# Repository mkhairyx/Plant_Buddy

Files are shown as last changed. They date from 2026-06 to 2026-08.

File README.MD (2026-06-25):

# Plant Buddy
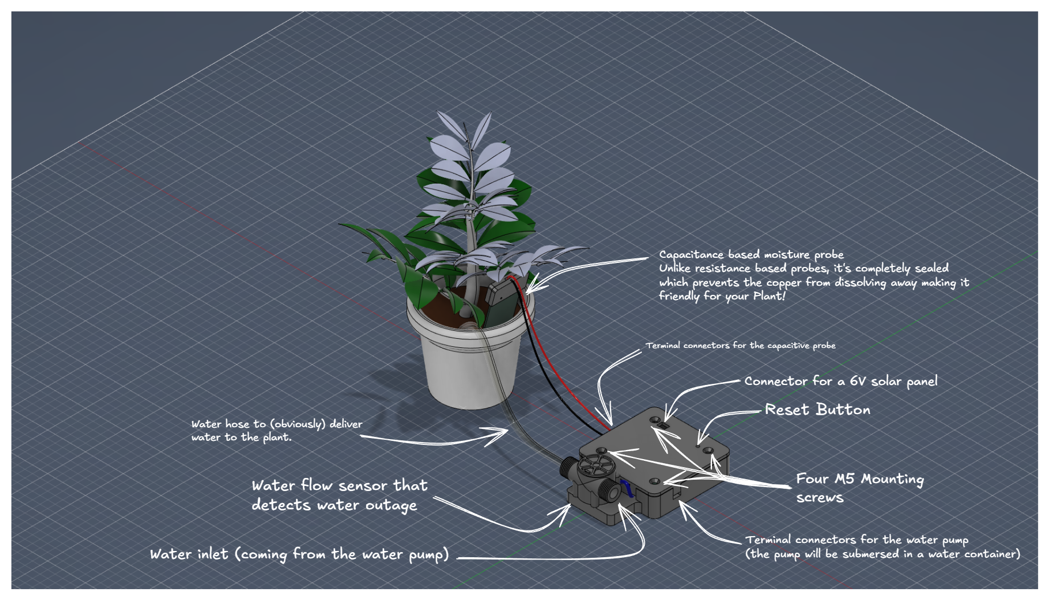
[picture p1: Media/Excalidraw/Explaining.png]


## The reason I made it
I have a plant at a remote location and I only go there once in a while, I was afraid that that plant might die because of the lack of water so I decided to make this device. It work by connecting a water pump to it, then it drives this pump every 20 days by default (configurable in the code). It measures the soil humidity for feedback to the user (which is delivered through SMS).

## The poster
zine

## Photos

|Schematic |PCB |3D View |Showcase |
|---|---|---|---|
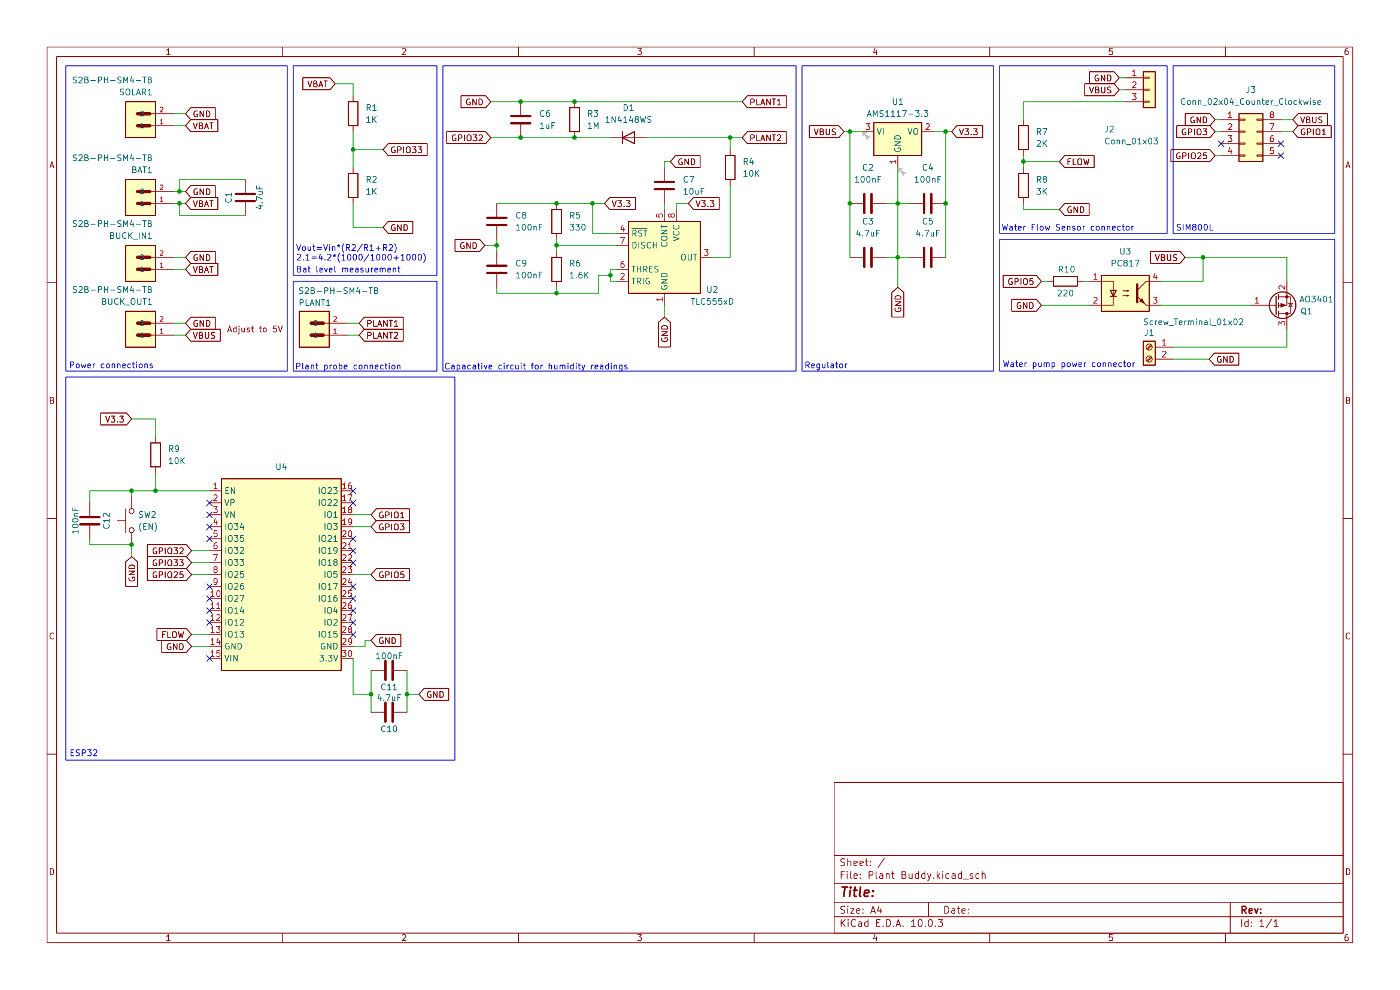
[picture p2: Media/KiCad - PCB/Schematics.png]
Schematics
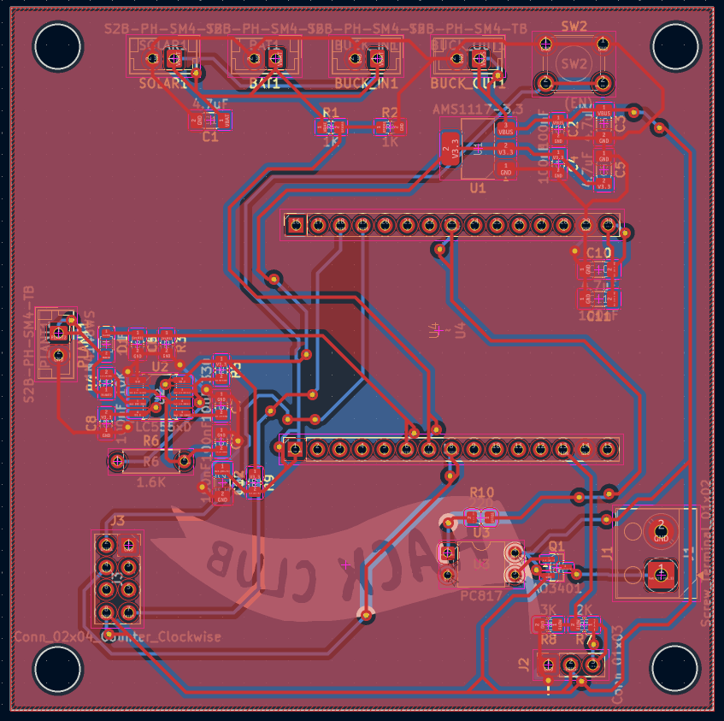
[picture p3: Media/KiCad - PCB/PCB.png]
PCB
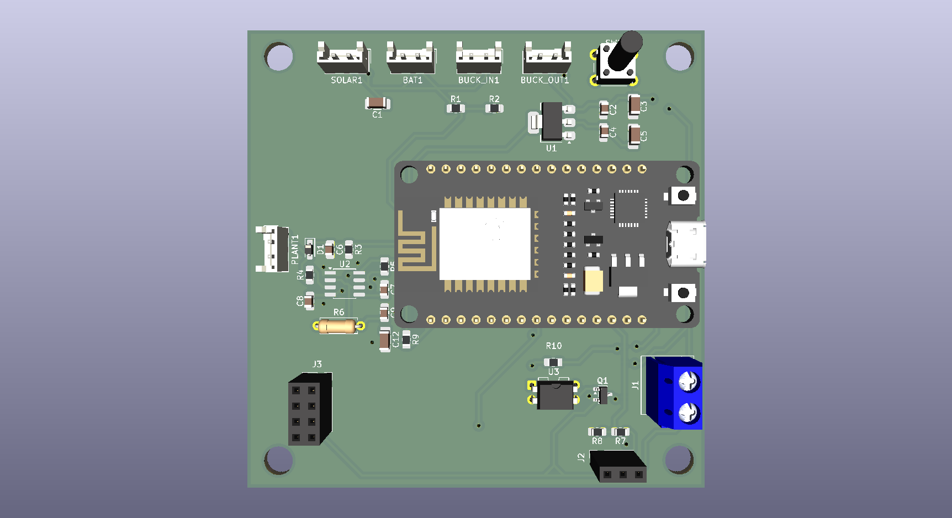
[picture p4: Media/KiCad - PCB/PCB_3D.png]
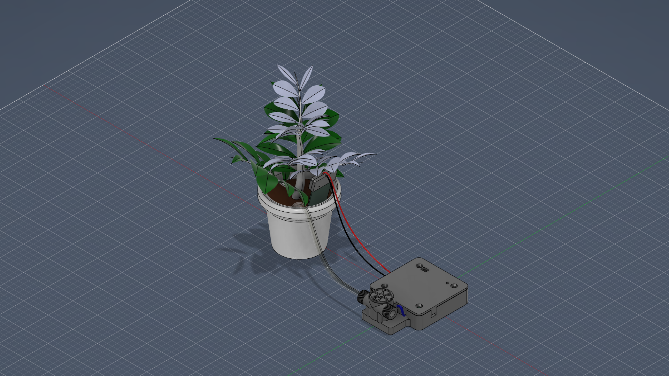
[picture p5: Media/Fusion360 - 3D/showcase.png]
Showcase
|||||

## Step files
All of the step files can be found [here](./Step_Files/).
<br>

## Firmware
### Compile and flash using the Arduino IDE
If you want to edit the code, compile it yourself, then flash it; you can download the arduino sketch [here](./Source/Firmware/Arduino/plant_buddy).

### Flash the firmware as is
If you want to flash the firmware as is, you can download it [here](./source/Firmware/Firmware). <br>
You can use [ESPWebTool](https://esptool.spacehuhn.com) to flash the firmware directly to the ESP32 using your browser.<br>
Note that there might be some changes between the Arduino code and the firmware as some changes were made.

## Device Operation
### Power supply
The device is powered a 3.7V recharge Li-Po battery.<br>
The battery is recharged daily using a 3W 6V mini solar panel connected to a mini solar charger which is connected to a buck converter to operate the ESP32.<br>
The ESP32 goes into Deep Sleep mode in between watering sessions to help decrease energy consumption.<br>

### Startup Notification

Whenever the ESP32 wakes up, it sends a status report to the user containing:

* Current battery level
* Current soil moisture level
* Watering interval
* Reason for waking up

Example:

```
The device just booted up!
Battery level: 87%
Soil humidity: 42%
Watering interval: 3 days

Boot reason: Watering cycle completed successfully.
Watering again in 3 days.
```

Possible boot reasons:

| Boot Reason | Description |
| --- | --- |
| Unknown Fault | The device restarted unexpectedly due to an unknown error. |
| Watering Cycle Completed | A watering cycle has just finished successfully, and a new countdown has started. |
| First Boot | The device has been powered on for the first time. |

## BOM
### BOM Table (components only)
|Name |Link |Cost per one (EGP) |Cost per one (USD) |Amount |Total cost|
|---|---|---|---|---|---|
|JST Connectors |https://www.ram-e-shop.com/shop/pw-m-pcb-2pin-pw-m-2-pin-polarized-male-jst-xh2-54-connector-for-pcb-6463| EGP 0.60 | $0.012 |5 | $0.060 |
|4.7uF Caps (1206) |https://lampatronics.com/product/smd-multilayer-ceramic-capacitor-1206-4-7uf-16v-1pcs| EGP 1.50 | $0.030 |4 | $0.120 |
|100nF Caps (0805) |https://lampatronics.com/product/smd-multilayer-ceramic-capacitor-0805-2012-104-100nf-50v-1pcs-2| EGP 1.00 | $0.020 |6 | $0.120 |
|1uF Caps (0805) |https://lampatronics.com/product/smd-ceramic-capacitor-0805-1051uf-50v-1pcs| EGP 1.50 | $0.030 |1 | $0.030 |
|10uF Caps (0805) |https://lampatronics.com/product/smd-multilayer-ceramic-capacitor-0805-10610uf-16v-1pcs| EGP 1.50 | $0.030 |1 | $0.030 |
|1N4148WS Diode |https://lampatronics.com/product/smd-diode-1n4148ws-10pcs| EGP 7.50 | $0.150 |1 | $0.150 |
|Screw terminal |https://www.ram-e-shop.com/shop/r-3-roseta-2pin-2-pin-pcb-screw-terminal-block-pitch-5mm-r-3-5854| EGP 3.00 | $0.060 |1 | $0.060 |
|Male headers |https://store.fut-electronics.com/products/male-pin-headers-standard-2-54-mm-40-pin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| EGP 10.00 | $0.200 |1 | $0.200 |
|Female headers |https://www.ram-e-shop.com/shop/ph35-1x4-female-ph35-pin-header-female-1x4-straight-2-54mm-6976| EGP 1.50 | $0.030 |2 | $0.060 |
|AO3401 (transistor for pump) |https://uge-one.com/product/ao3401-sot23-general-purpose-p-channel-mosfet-smd-transistor-sot-23/| EGP 3.00 | $0.060 |1 | $0.060 |
|1K ohm Resistors |https://lampatronics.com/product/smd-resistor-1kohm-102-0805-10pcs| EGP 2.00 | $0.040 |1 | $0.040 |
|1M ohm Resistors |https://lampatronics.com/product/smd-resistor-1mohm-105-0805-10pcs| EGP 2.00 | $0.040 |1 | $0.040 |
|10K ohm Resistors |https://lampatronics.com/product/smd-resistor-10kohm-103-0805-10pcs| EGP 2.00 | $0.040 |1 | $0.040 |
|330 ohm Resistors |https://lampatronics.com/product/smd-resistor-330ohm-331-0805-10pcs| EGP 2.00 | $0.040 |1 | $0.040 |
|1.5Kohm Resistors |https://lampatronics.com/product/resistor-1-5k-ohm-1-4w-4pcs-2| EGP 0.30 | $0.006 |1 | $0.006 |
|2K ohm Resistors |https://lampatronics.com/product/smd-resistor-2kohm-202-0805-10pcs| EGP 2.00 | $0.040 |1 | $0.040 |
|3K ohm Resistors |https://lampatronics.com/product/smd-resistor-3kohm-302-0805-10pcs| EGP 2.00 | $0.040 |1 | $0.040 |
|220 ohm Resistors |https://lampatronics.com/product/smd-resistor-220ohm-221-0805-10pcs| EGP 2.00 | $0.040 |1 | $0.040 |
|Reset Push Button |https://lampatronics.com/product/push-button-4pin-long-6x6x13mm| EGP 1.50 | $0.030 |1 | $0.030 |
|Voltage Regulator |https://lampatronics.com/product/ams1117-33v-sot-223-33v-linear-voltage-regulator| EGP 2.00 | $0.040 |1 | $0.040 |
|TLC555xD (Capacitive soil readings) |https://uge-one.com/product/tlc555cdr-low-power-cmos-timer-ic-smd-sop8/| EGP 35.00 | $0.700 |1 | $0.700 |
|PC817 optocoupler |https://lampatronics.com/product/pc817-optocoupler-dip-4| EGP 1.25 | $0.025 |1 | $0.025 |
|ESP32 DevKit |https://lampatronics.com/product/esp32-30pin-development-board-wifi-and-bluetooth| EGP 325.00 | $6.500 |1 | $6.500 |
|Water Pump |https://www.ram-e-shop.com/shop/dc-pump-6vdc-water-pump-3-6vdc-mini-120l-h-7422| EGP 45.00 | $0.900 |1 | $0.900 |
|Hose (inner d: 6mm , outer d: 8mm) 1 Meter |https://lampatronics.com/product/flexible-clear-hose-tube-pipe-6mm-airwater-pump-pvc| EGP 15.00 | $0.300 |2 | $0.600 |
|Water Flow sensor |https://store.fut-electronics.com/products/water-flow-rate-sensor?_pos=8&_sid=5e9c09df8&_ss=r| EGP 260.00 | $5.200 |1 | $5.200 |
|SIM800L GSM Module |https://store.fut-electronics.com/collections/gsm-gprs/products/sim800l-gprs-gsm-module-esp-core-board-with-built-in-antenna| EGP 280.00 | $5.600 |1 | $5.600 |
|3W 6V Mini Solar Panel |https://store.fut-electronics.com/products/solar-cell-129-x-129-mm-3w?_pos=3&_sid=fdb2b11fe&_ss=r| EGP 155.00 | $3.100 |1 | $3.100 |
|Mini solar charger |https://store.fut-electronics.com/products/solar-usb-charger-for-lithium-batteries-lipo-rider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| EGP 160.00 | $3.200 |1 | $3.200 |
|Battery |https://store.fut-electronics.com/products/3-7v-rechargeable-polymer-lithium-ion-battery-ecocell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| EGP 125.00 | $2.500 |1 | $2.500 |
|M5 Screws |https://store.fut-electronics.com/products/screw-m5x25mm-hexagonal-head?_pos=5&_sid=c4191184f&_ss=r| EGP 2.00 | $0.040 |4 | $0.160 |
| | | | | | |
| | | | |Whole Total| $29.731  |

### Quotes
[JLCPCB](https://jlcpcb.com) : $57.12
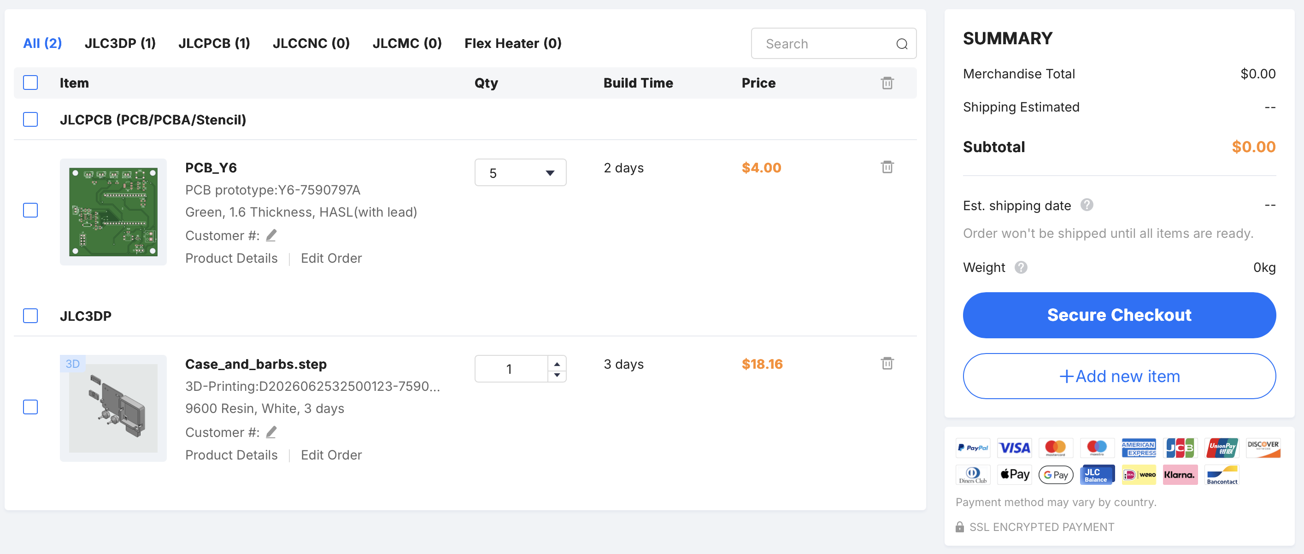
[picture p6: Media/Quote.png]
Quote

<br>
Note that local manufacturers might have different prices.

## Notes
A future V2 is planned with support for multiple probes, improved power efficiency, and user-requested status updates.

> Made and designed by [@mkhairyx](https://github.com/mkhairyx).<br>
Supported by [Fallout](https://fallout.hackclub.com/) and [Hack Club](https://hackclub.com).<br>

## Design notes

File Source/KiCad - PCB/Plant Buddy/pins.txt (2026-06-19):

gpio 33 for battery voltage -
gpio 32 for soil readings -
gpio 5 for pump motor -
gpio 3 for gsm_tx -
gpio 1 for gsm_rx -
gpio 13 for flow -
gpio 25 for ring ping -

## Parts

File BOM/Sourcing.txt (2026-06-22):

- water pump: https://www.ram-e-shop.com/shop/dc-pump-6vdc-water-pump-3-6vdc-mini-120l-h-7422
- hose: https://lampatronics.com/product/flexible-clear-hose-tube-pipe-6mm-airwater-pump-pvc
- Flow sensor: https://store.fut-electronics.com/products/water-flow-rate-sensor?_pos=8&_sid=5e9c09df8&_ss=r
- SIM800L: https://store.fut-electronics.com/collections/gsm-gprs/products/sim800l-gprs-gsm-module-esp-core-board-with-built-in-antenna
- 6w solar: https://store.fut-electronics.com/products/solar-cell-129-x-129-mm-3w?_pos=3&_sid=fdb2b11fe&_ss=r
- Mini solar charger: https://store.fut-electronics.com/products/solar-usb-charger-for-lithium-batteries-lipo-rider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
- JST: https://www.ram-e-shop.com/shop/pw-m-pcb-2pin-pw-m-2-pin-polarized-male-jst-xh2-54-connector-for-pcb-6463
step up module: https://lampatronics.com/product/dc-dc-step-up-boost-converter-module-xl6009-3a
1N4148WS: https://makerselectronics.com/product/smd-switching-diode-1n4148ws-t4-100v-independent-type-1-25v150ma-4ns-150ma-sod-323/
- 555: https://uge-one.com/product/tlc555cdr-low-power-cmos-timer-ic-smd-sop8/
- terminal connector: https://www.ram-e-shop.com/shop/r-3-roseta-2pin-2-pin-pcb-screw-terminal-block-pitch-5mm-r-3-5854
- Female headers : https://www.ram-e-shop.com/shop/ph35-1x4-female-ph35-pin-header-female-1x4-straight-2-54mm-6976
- 4.7uF: https://lampatronics.com/product/smd-multilayer-ceramic-capacitor-1206-4-7uf-16v-1pcs
- 100nF: https://lampatronics.com/product/smd-multilayer-ceramic-capacitor-0805-2012-104-100nf-50v-1pcs-2
- 1uF: https://lampatronics.com/product/smd-ceramic-capacitor-0805-1051uf-50v-1pcs
- 10uF: https://lampatronics.com/product/smd-multilayer-ceramic-capacitor-0805-10610uf-16v-1pcs
- 1N4148WS: https://lampatronics.com/product/smd-diode-1n4148ws-10pcs
- AO3401: https://uge-one.com/product/ao3401-sot23-general-purpose-p-channel-mosfet-smd-transistor-sot-23/
- 1Kohm: https://lampatronics.com/product/smd-resistor-1kohm-102-0805-10pcs
- 1Mohm: https://lampatronics.com/product/smd-resistor-1mohm-105-0805-10pcs
- 10Kohm: https://lampatronics.com/product/smd-resistor-10kohm-103-0805-10pcs
- 330ohm: https://lampatronics.com/product/smd-resistor-330ohm-331-0805-10pcs
- 1.5Kohm: https://lampatronics.com/product/resistor-1-5k-ohm-1-4w-4pcs-2
- 2Kohm: https://lampatronics.com/product/smd-resistor-2kohm-202-0805-10pcs
- 3Kohm: https://lampatronics.com/product/smd-resistor-3kohm-302-0805-10pcs
- 220ohm : https://lampatronics.com/product/smd-resistor-220ohm-221-0805-10pcs
- RST button: https://lampatronics.com/product/push-button-4pin-long-6x6x13mm
- AMS1117-3.3: https://lampatronics.com/product/ams1117-33v-sot-223-33v-linear-voltage-regulator
- PC817: https://lampatronics.com/product/pc817-optocoupler-dip-4
- ESP32: https://lampatronics.com/product/esp32-30pin-development-board-wifi-and-bluetooth
- Battery: https://store.fut-electronics.com/products/3-7v-rechargeable-polymer-lithium-ion-battery-ecocell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
- four M5 screws: https://store.fut-electronics.com/products/screw-m5x25mm-hexagonal-head?_pos=5&_sid=c4191184f&_ss=r

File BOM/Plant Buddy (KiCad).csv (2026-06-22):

Reference | Qty | Value | Footprint
BAT1,BUCK_IN1,BUCK_OUT1,PLANT1,SOLAR1 | 5 | S2B-PH-SM4-TB | Connector_JST:JST_EH_B2B-EH-A_1x02_P2.50mm_Vertical
C1,C3,C5,C10 | 4 | 4.7uF | Capacitor_SMD:C_1206_3216Metric_Pad1.33x1.80mm_HandSolder
C2,C4,C8,C9 | 4 | 100nF | Capacitor_SMD:C_0805_2012Metric_Pad1.18x1.45mm_HandSolder
C6 | 1 | 1uF | Capacitor_SMD:C_0805_2012Metric_Pad1.18x1.45mm_HandSolder
C7 | 1 | 10uF | Capacitor_SMD:C_0805_2012Metric_Pad1.18x1.45mm_HandSolder
C11,C12 | 2 | 100nF | Capacitor_SMD:C_1206_3216Metric_Pad1.33x1.80mm_HandSolder
D1 | 1 | 1N4148WS | Diode_SMD:D_SOD-323_HandSoldering
J1 | 1 | Screw_Terminal_01x02 | TerminalBlock_Altech:Altech_AK100_1x02_P5.00mm
J2 | 1 | Conn_01x03 | Connector_PinSocket_2.54mm:PinSocket_1x03_P2.54mm_Vertical
J3 | 1 | Conn_02x04_Counter_Clockwise | Connector_PinSocket_2.54mm:PinSocket_2x04_P2.54mm_Vertical
Q1 | 1 | AO3401 | Package_TO_SOT_SMD:SOT-23
R1,R2 | 2 | 1K | Resistor_SMD:R_0805_2012Metric_Pad1.20x1.40mm_HandSolder
R3 | 1 | 1M | Resistor_SMD:R_0805_2012Metric_Pad1.20x1.40mm_HandSolder
R4,R9 | 2 | 10K | Resistor_SMD:R_0805_2012Metric_Pad1.20x1.40mm_HandSolder
R5 | 1 | 330 | Resistor_SMD:R_0805_2012Metric_Pad1.20x1.40mm_HandSolder
R6 | 1 | 1.6K | Resistor_THT:R_Axial_DIN0207_L6.3mm_D2.5mm_P7.62mm_Horizontal
R7 | 1 | 2K | Resistor_SMD:R_0805_2012Metric_Pad1.20x1.40mm_HandSolder
R8 | 1 | 3K | Resistor_SMD:R_0805_2012Metric_Pad1.20x1.40mm_HandSolder
R10 | 1 | 220 | Resistor_SMD:R_0805_2012Metric_Pad1.20x1.40mm_HandSolder
SW2 | 1 | (EN) | Button_Switch_THT:SW_PUSH_6mm_H13mm
U1 | 1 | AMS1117-3.3 | Package_TO_SOT_SMD:SOT-223-3_TabPin2
U2 | 1 | TLC555xD | Package_SO:SOP-8_3.76x4.96mm_P1.27mm
U3 | 1 | PC817 | Package_DIP:DIP-4_W7.62mm
U4 | 1 |  | Library:ESP32 DevKit

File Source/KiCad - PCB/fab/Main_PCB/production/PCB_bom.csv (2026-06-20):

Designator | Footprint | Quantity | Value | LCSC Part #
BAT1, BUCK_IN1, BUCK_OUT1, PLANT1, SOLAR1 | JST_EH_B2B-EH-A_1x02_P2.50mm_Vertical | 5 | S2B-PH-SM4-TB
C1, C10, C3, C5 | 1206 | 4 | 4.7uF
C11, C12 | 1206 | 2 | 100nF
C2, C4, C8, C9 | 0805 | 4 | 100nF
C6 | 0805 | 1 | 1uF
C7 | 0805 | 1 | 10uF
D1 | D_SOD-323_HandSoldering | 1 | 1N4148WS
J1 | Altech_AK100_1x02_P5.00mm | 1 | Screw_Terminal_01x02
J2 | PinSocket_1x03_P2.54mm_Vertical | 1 | Conn_01x03
J3 | PinSocket_2x04_P2.54mm_Vertical | 1 | Conn_02x04_Counter_Clockwise
Q1 | SOT-23 | 1 | AO3401
R1, R2 | 0805 | 2 | 1K
R10 | 0805 | 1 | 220
R3 | 0805 | 1 | 1M
R4, R9 | 0805 | 2 | 10K
R5 | 0805 | 1 | 330
R6 | R_Axial_DIN0207_L6.3mm_D2.5mm_P7.62mm_Horizontal | 1 | 1.6K
R7 | 0805 | 1 | 2K
R8 | 0805 | 1 | 3K
SW2 | SW_PUSH_6mm_H13mm | 1 | (EN)
U1 | SOT-223-3_TabPin2 | 1 | AMS1117-3.3
U2 | SOP-8_3.76x4.96mm_P1.27mm | 1 | TLC555xD
U3 | DIP-4_W7.62mm | 1 | PC817
U4 | ESP32 DevKit | 1 | ~

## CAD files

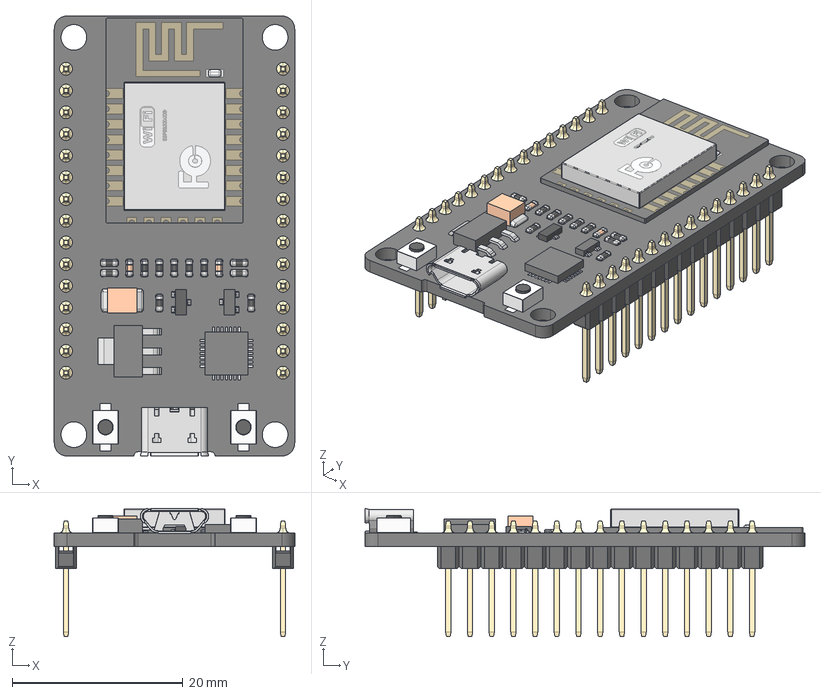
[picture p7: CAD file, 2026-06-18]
Source/Online 3D models/esp32_dev_kit_v1_asm.stp
28.1 x 51.5 x 15.0 mm
PCB
PIN x 30
WIFI_CARD_2
RECTANGULARCHIP_2
MICROCHIP_2
TANCHIP_2
TRANSISTOR_3-LEG_2
RESISTOR1_2 x 11
RESISTOR2-32_2 x 2
TRANSISTOR_3-LEG2_2
BUTTONFLASH-13_2 x 2
BUTTONFLASH-14_2 x 2
USB_SOCKET_2

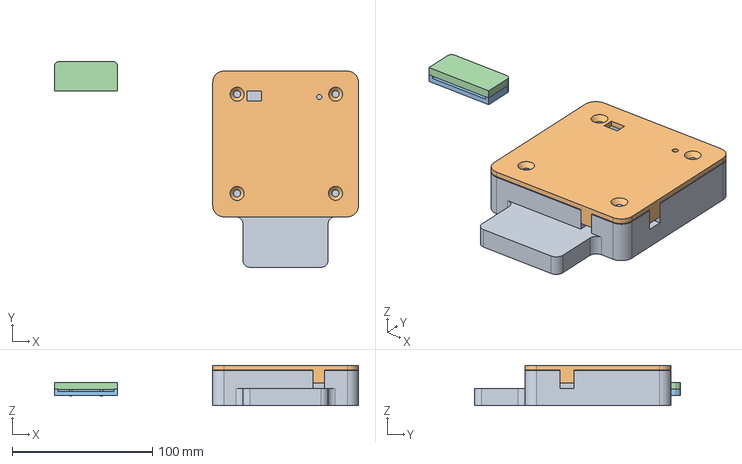
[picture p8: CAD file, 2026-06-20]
Step_Files/Assembled/assembled.step
216.9 x 146.7 x 28.6 mm

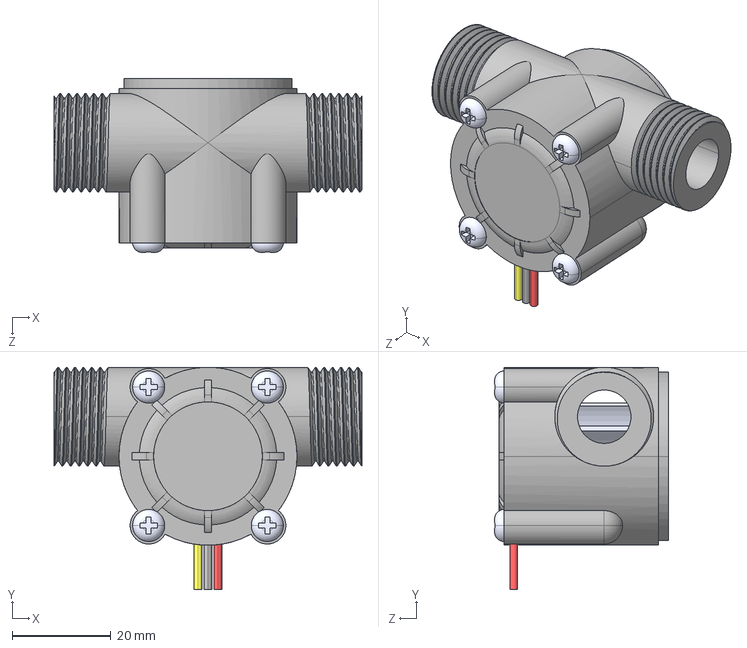
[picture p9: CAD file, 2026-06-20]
Source/Blender - Renders/assets/water-flow-sensor-yf-s201-1.snapshot.2/Water Flow Sensor YF-S201.STEP
62.3 x 45.0 x 35.2 mm

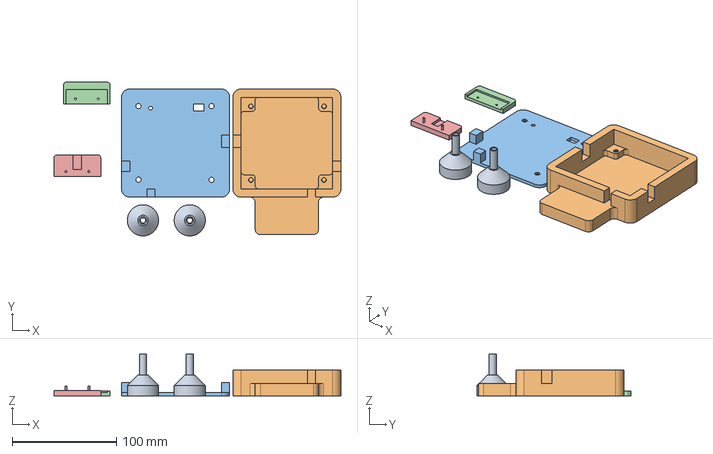
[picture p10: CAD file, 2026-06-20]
Source/Fusion 360 - 3D/casenbarbs.step
275.9 x 148.0 x 40.0 mm
Barb x 2

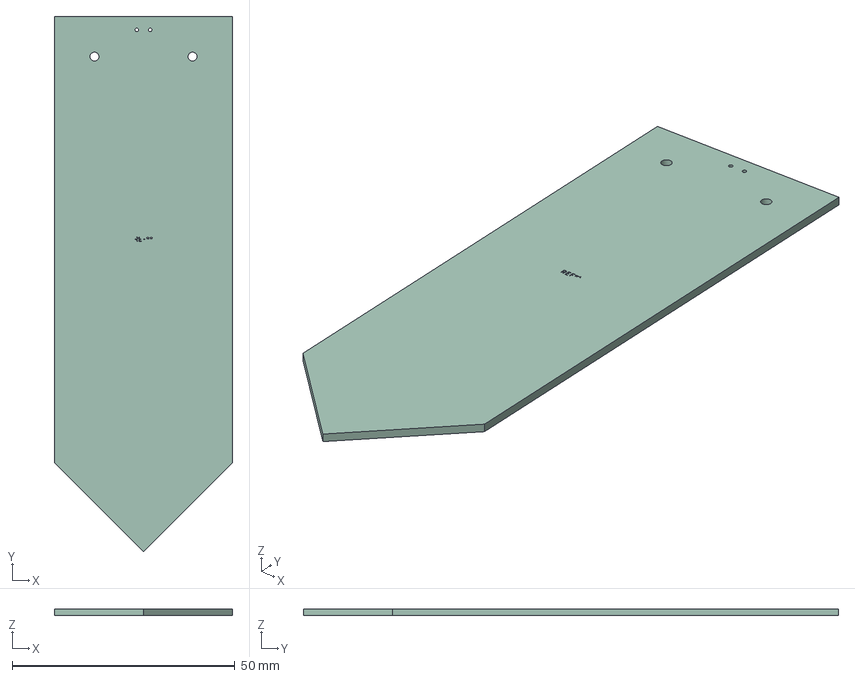
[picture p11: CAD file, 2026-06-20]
Source/KiCad - PCB/PCB_step/probe.step
40.0 x 120.0 x 1.58 mm
Plant Buddy - Probe_silkscreen
Plant Buddy - Probe_PCB

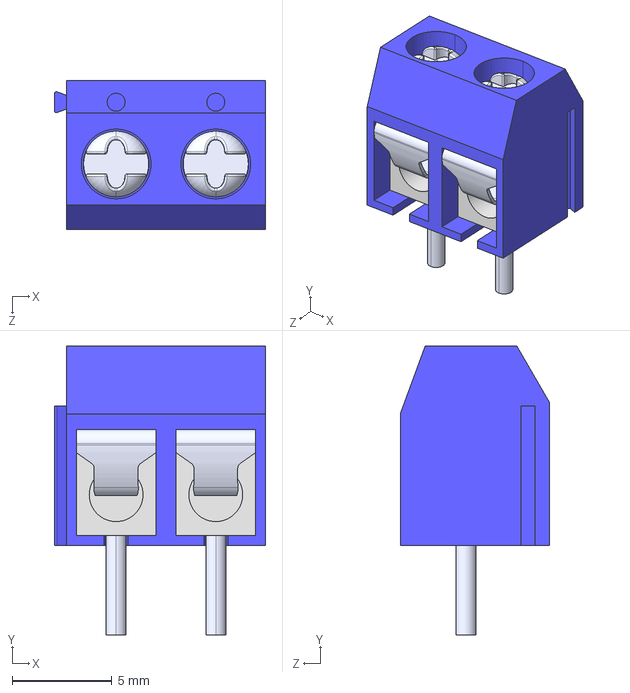
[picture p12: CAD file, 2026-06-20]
Source/KiCad - PCB/Plant Buddy/3d/KF301-2P--3DModel-STEP-510211.STEP
10.6 x 14.5 x 7.50 mm

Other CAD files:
Step_Files/Case_and_barbs/Case_and_barbs.step
Source/Blender - Renders/assets/water-flow-sensor-yf-s201-1.snapshot.2/Water Flow Sensor YF-S201.SLDPRT
Source/blender/scene.blend

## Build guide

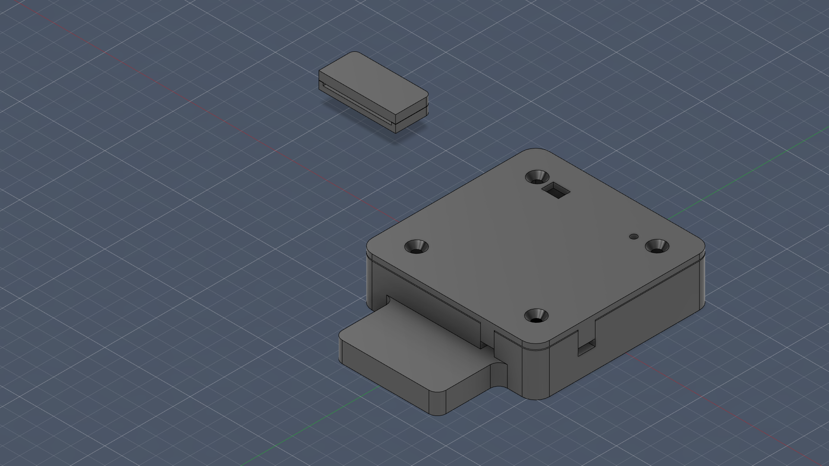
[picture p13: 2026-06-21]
Media/Fusion360 - 3D/Assembled.png

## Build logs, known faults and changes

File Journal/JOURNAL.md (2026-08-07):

# Plant Buddy

---
title: Plant Buddy
author: Mo
description: A device that waters your plants, checks the humidity of the soil of each one of them, powered by solar power, and detects when there's no source of water.<br>
created_at: "2026-06-16" <br>
Total time spent on project: 20h 56m

---

## Entry 1
**Total time spent: 2h 2m**
- Author: Mo
- Created At: 2026-06-17 05:17:53

### Content

I first sketched out my thoughts on Excalidraw then start making the schematics off of it:

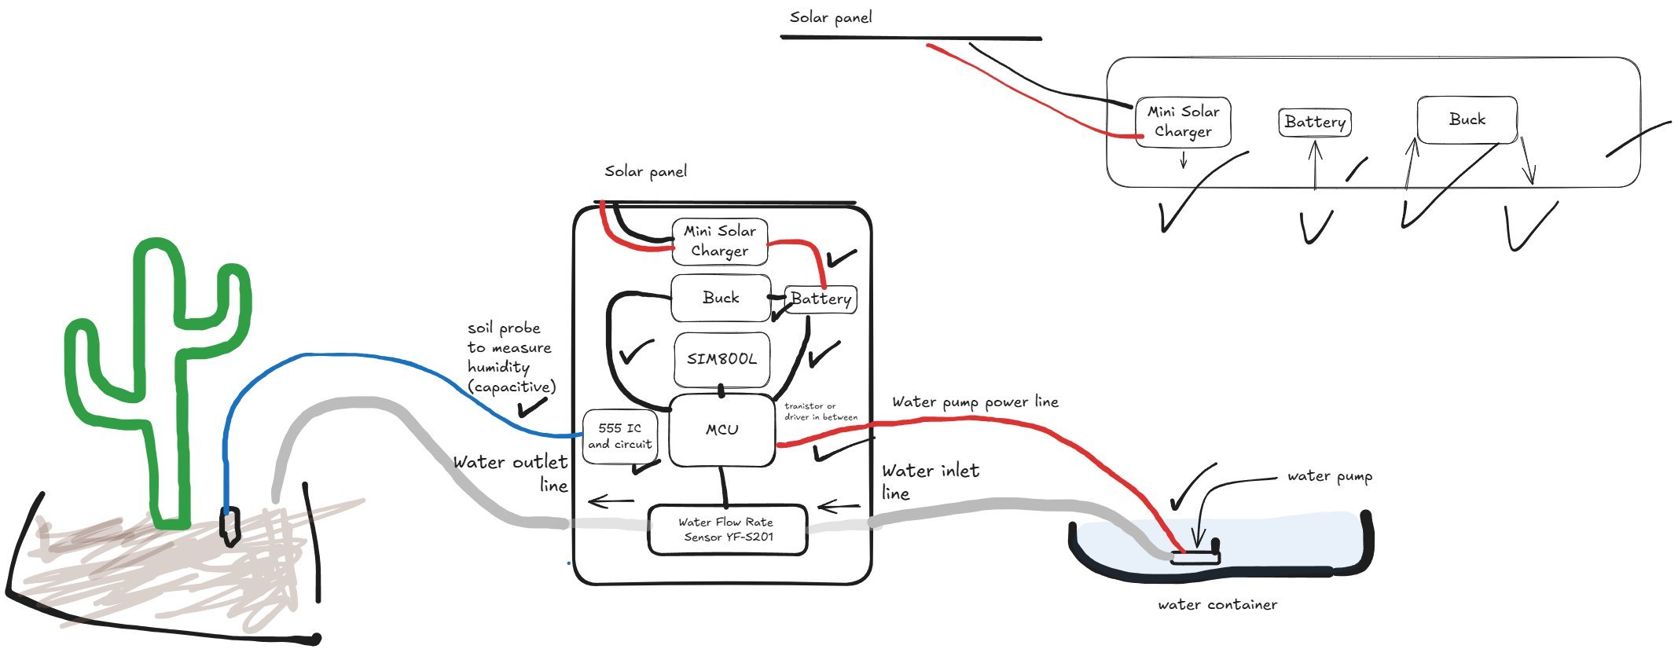
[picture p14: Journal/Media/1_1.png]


I finished a part of the schematics but there's a lot left to do.
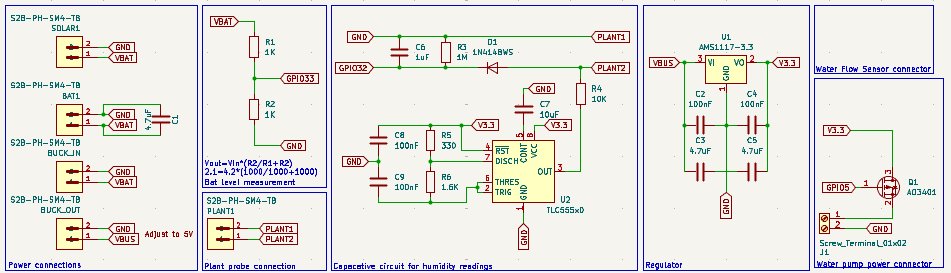
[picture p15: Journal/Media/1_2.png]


### Recording Links

- https://lookout.hackclub.com/api/media/44d95b6e-832b-497f-ad53-9a4256ca0aa4/video.mp4

## Entry 2
**Total time spent: 17min**
- Author: Mo
- Created At: 2026-06-17T06:57:26Z

### Content

Added a connector the water flow sensor (mind you that it runs on 5 volts so I had to make step up board output 5V instead of 3.3V. I'll be using the LDO's output as the VBUS for the ESP32 and other components running on 3.3V)
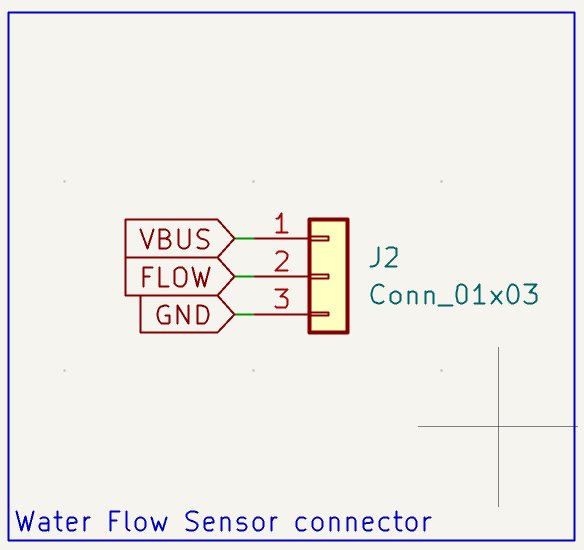
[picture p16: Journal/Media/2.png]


### Recording Links

- https://lookout.hackclub.com/api/media/3beeefda-2175-451c-a2ec-e248ded411d0/video.mp4

## Entry 3
**Total time spent: 3h 55m**
- Author: Mo
- Created At: 2026-06-18T00:29:38Z

### Content

Made a lot of things in one day.
I finished the schematics, the PCB, and what's left for now is the Case and an adapter for the hose as it's too small for the water flow sensor.
Here's what the PCB and the Schematics look like:
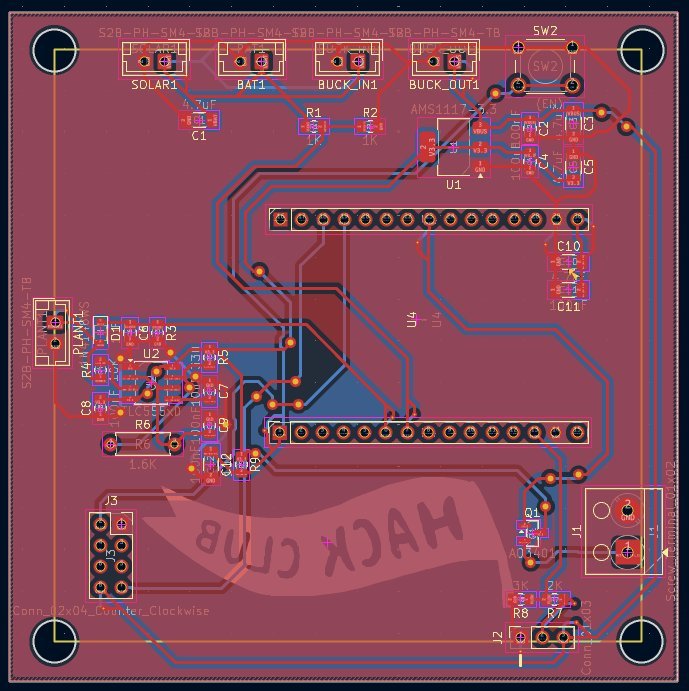
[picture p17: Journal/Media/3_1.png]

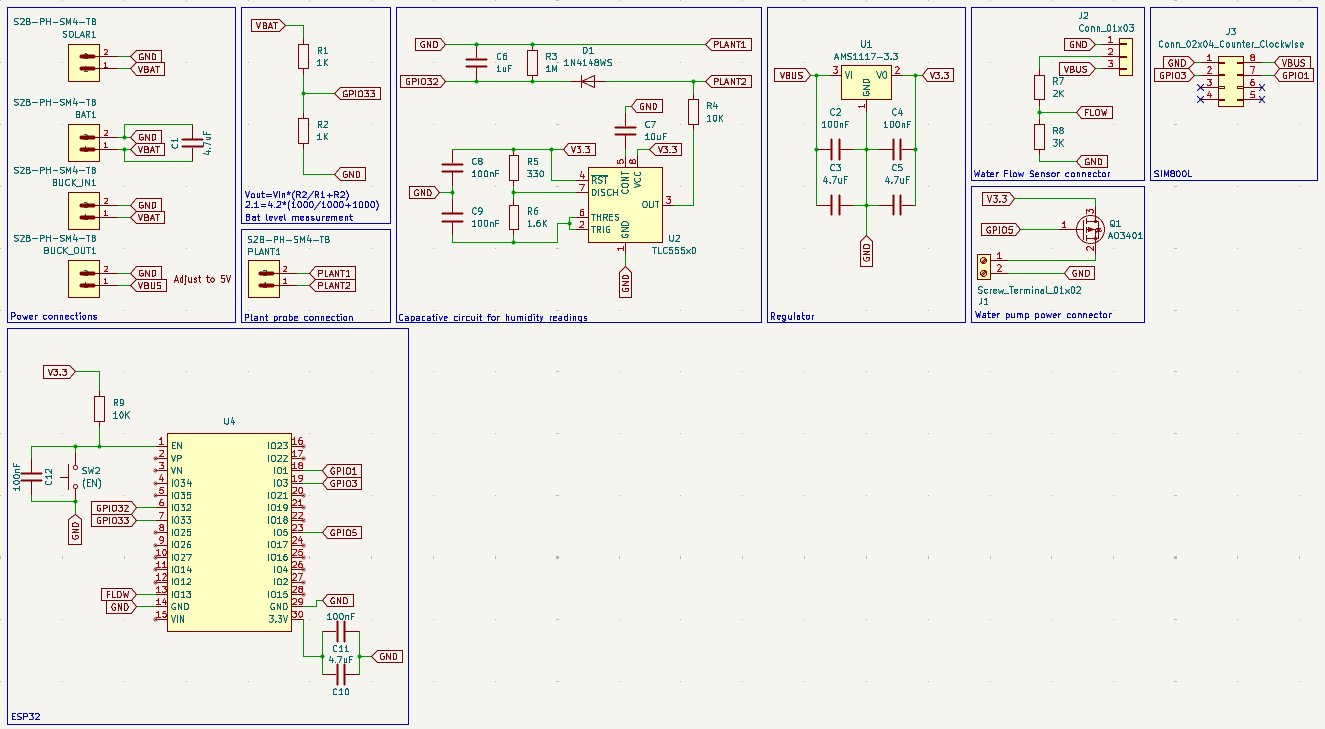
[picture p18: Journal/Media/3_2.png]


I used the ESP32 devkit as it's more available in my country and cheaper than the wroom module. Plus it helps with reparability. 

### Recording Links

- https://lookout.hackclub.com/api/media/27bd34d5-f5ff-4612-8b61-ed291d3221e3/video.mp4

## Entry 4
**Total time spent: 1h**
- Author: Mo
- Created At: 2026-06-20T01:20:02Z

### Content

I have connected a ring line so the esp32 can wake up whenever the sim800l module receives a message. Also I'm routing the tracks to both the front and back sides of copper layers as my manufacturer doesn't have plated through holes.

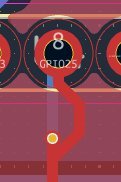
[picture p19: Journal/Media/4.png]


for now, I'm still figuring out how the codes will work and there's a lot of undecided things.

### Recording Links

- https://lookout.hackclub.com/api/media/fcdc8102-188f-40f8-956a-141435dee443/video.mp4

## Entry 5
**Total time spent: 3h 26m**
- Author: Mo
- Created At: 2026-06-20T07:15:06Z

### Content

Extremely exhausted.
I did the code, made it somewhat basic (no replying to user messages, no measuring for the amount of water poured since I need the sensor to be physically available so I can calibrate the firmware to it). But I believe it is sufficient for now.
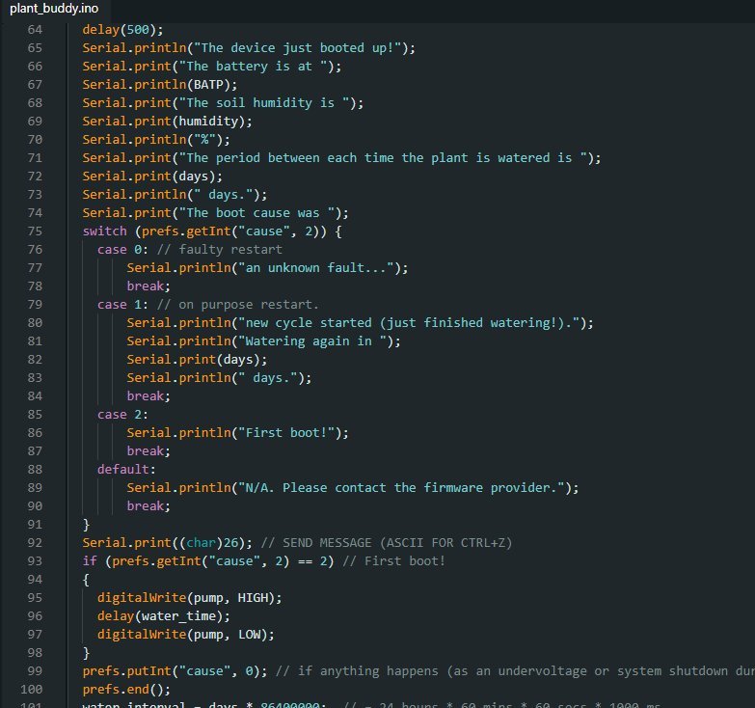
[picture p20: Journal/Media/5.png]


### Recording Links

- https://lookout.hackclub.com/api/media/376545c8-d42d-4711-8be1-f17a7eec2e2d/video.mp4

## Entry 6
**Total time spent: 3h 49m**
- Author: Mo
- Created At: 2026-06-20T11:34:44Z

### Content

I finished the 3D model. what's left for now is the readme, the zine poster, and some 3D renders for the poster.

Here's how the device looks like:
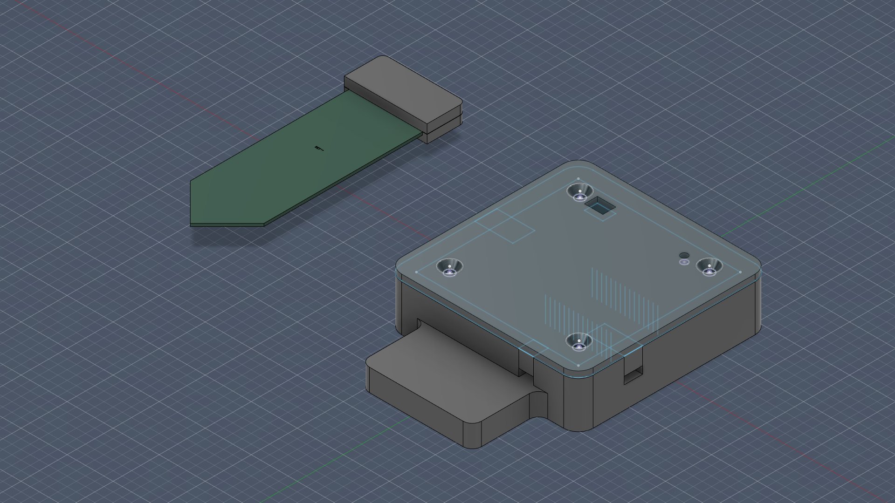
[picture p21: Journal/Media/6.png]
show case v1.png


### Recording Links

- https://lookout.hackclub.com/api/media/ab6cfb18-3d7e-450d-b56a-0922fbad71be/video.mp4

## Entry 7
**Total time spent: 1h 37m**
- Author: Mo
- Created At: 2026-06-20T13:21:14Z

### Content

Me and blender are going through the same thing rn (both of us are crashing out):
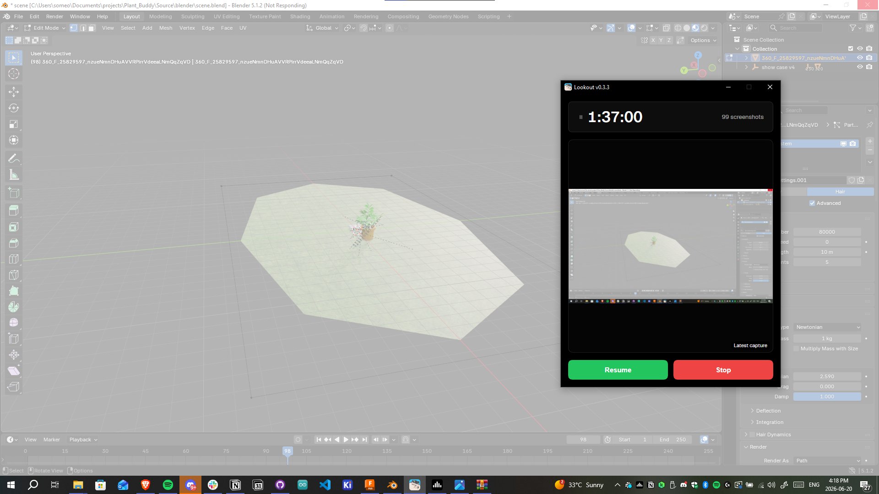
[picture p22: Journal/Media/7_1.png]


Beside that, I have finished the showcase on fusion360 and I might be using this for the poster instead of blender:
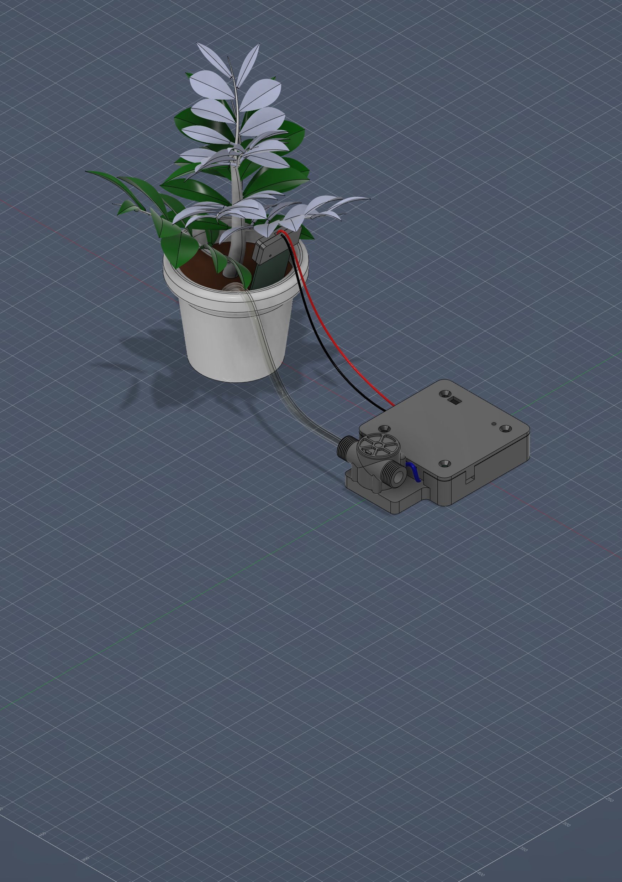
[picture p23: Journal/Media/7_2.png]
show case v5.png

(it's imperfect but I will improve it)

### Recording Links

- https://lookout.hackclub.com/api/media/a747f22e-693e-41f7-b371-261eb6d79cd6/video.mp4

## Entry 8
**Total time spent: 1h 4m**
- Author: Mo
- Created At: 2026-06-21T01:42:23Z

### Content

Finished the render!

it was kind of hard as my device is 5 years old with a somewhat dated graphics card, but I managed to work with it!

Here's how the render looks like:
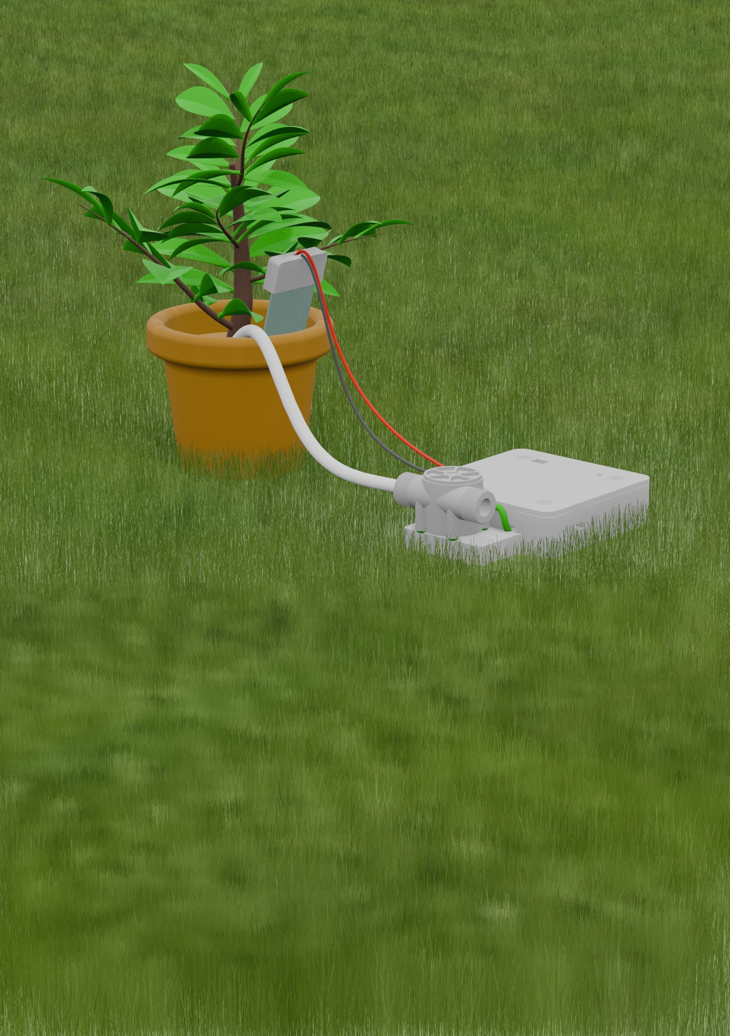
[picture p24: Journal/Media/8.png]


I wanted to add more grass as it would look more realistic but my device can't handle it.

I might modify the texture later and then re-render it. But for now, I'm satisfied with this render.

### Recording Links

- https://lookout.hackclub.com/api/media/40ab7a47-8c26-4372-bd49-37252a3c831d/video.mp4

## Entry 9
**Total time spent: 30min**
- Author: Mo
- Created At: 2026-06-21T02:49:51Z

### Content

I modified the texture's a bit so they look better.

I made the water tube transparent, added better color to the wires connected to the probe that's in the soil, and I fixed some things like the cable of the flow sensor being green (made it black), and the screw of the flow sensor were also green (made them black).

Here's what the render looks like:

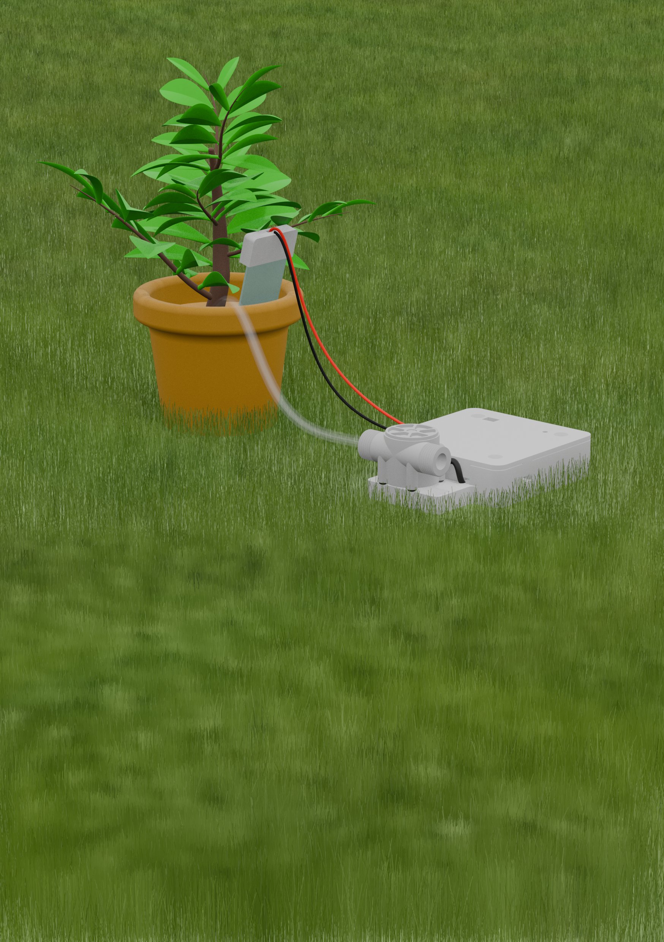
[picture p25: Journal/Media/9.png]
render 2.png


### Recording Links

- https://lookout.hackclub.com/api/media/63ef874c-4d73-4984-b8f3-b1262206fcad/video.mp4

## Entry 10
**Total time spent: 35min**
- Author: Mo
- Created At: 2026-06-21T08:21:33Z

### Content

Added all the required files.

I made sure all the files are available (like the Fusion files, media, etc.)
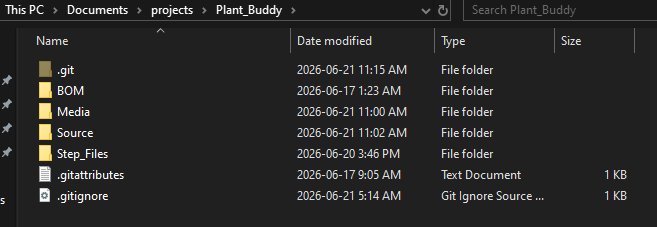
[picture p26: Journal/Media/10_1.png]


What's left now is the Zine poster, and the README.

Also made this drawing so reviewers can understand how everything works better:
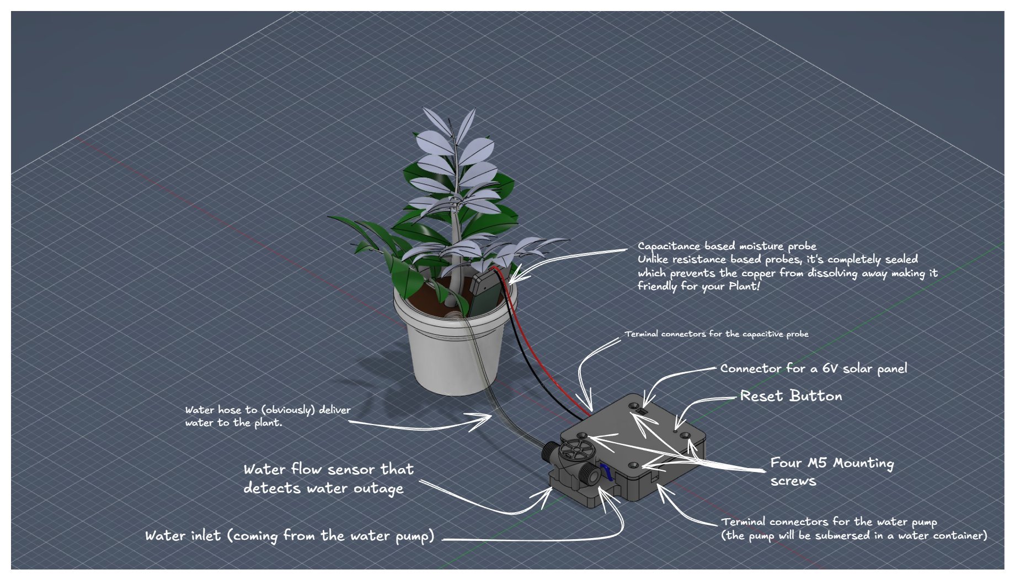
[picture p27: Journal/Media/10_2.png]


### Recording Links

- https://lookout.hackclub.com/api/media/1dafa0e2-5839-47d0-afe5-de055ddee4ca/video.mp4

## Entry 11
**Total time spent: 1h 12m**
- Author: Mo
- Created At: 2026-06-23T03:46:48Z

### Content

I finished the BOM and changed the 1.6Kohm resistor (that is used with the 555 timer for capacitive soil moisture readings) with a 1.5Kohm resistor. 

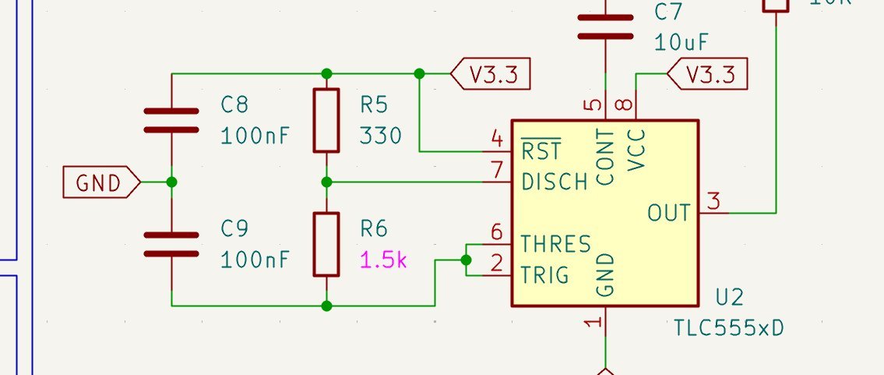
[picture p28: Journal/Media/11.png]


The reason I changed it is that I wasn't able to find 1.6Kohm resistors anywhere.

### Recording Links

- https://lookout.hackclub.com/api/media/fbb3ce3d-9b23-4fc6-85db-722628a7d8d8/video.mp4

## Entry 12
**Total time spent: 1h 29m**
- Author: Mo
- Created At: 2026-06-25T07:52:30Z

### Content

Finished the zine and the README!

There's nothing much to say for this journal.

Here's the README contents:

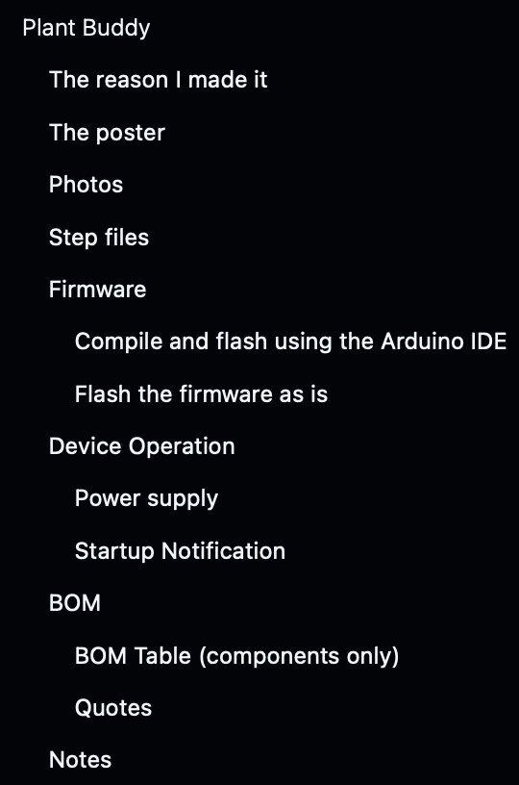
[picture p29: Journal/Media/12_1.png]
Screenshot 2026-06-25 at 10.50.21.png


Here's the zine poster:

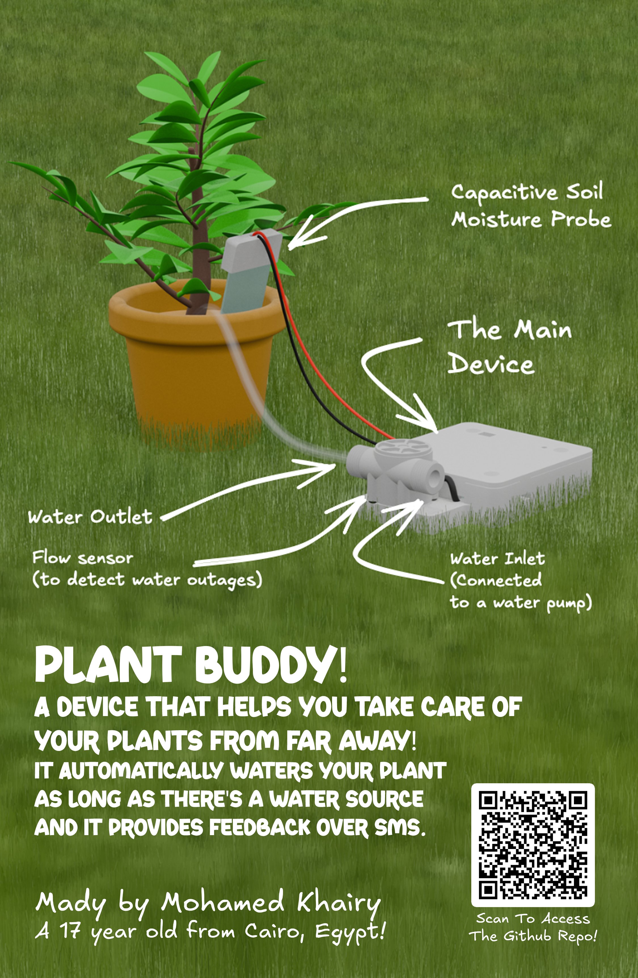
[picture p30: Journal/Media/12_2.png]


### Recording Links

- https://lookout.hackclub.com/api/media/d3a80291-8f6e-4dda-83fb-e65016a85ed3/video.mp4

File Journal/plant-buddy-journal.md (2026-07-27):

# Plant Buddy

- Exported at: 2026-07-27T00:40:03Z
- Project ID: 4602
- Entries: 12

## Entry 1
- ID: 14694
- Author: Mo
- Created At: 2026-06-17T05:17:53Z

### Content

I first sketched out my thoughts on Excalidraw then start making the schematics off of it:



I finished a part of the schematics but there's a lot left to do.


### Recording Links

- https://lookout.hackclub.com/api/media/44d95b6e-832b-497f-ad53-9a4256ca0aa4/video.mp4

## Entry 2
- ID: 14709
- Author: Mo
- Created At: 2026-06-17T06:57:26Z

### Content

Added a connector the water flow sensor (mind you that it runs on 5 volts so I had to make step up board output 5V instead of 3.3V. I'll be using the LDO's output as the VBUS for the ESP32 and other components running on 3.3V)


### Recording Links

- https://lookout.hackclub.com/api/media/3beeefda-2175-451c-a2ec-e248ded411d0/video.mp4

## Entry 3
- ID: 14888
- Author: Mo
- Created At: 2026-06-18T00:29:38Z

### Content

Made a lot of things in one day.
I finished the schematics, the PCB, and what's left for now is the Case and an adapter for the hose as it's too small for the water flow sensor.
Here's what the PCB and the Schematics look like:



I used the ESP32 devkit as it's more available in my country and cheaper than the wroom module. Plus it helps with reparability. 

### Recording Links

- https://lookout.hackclub.com/api/media/27bd34d5-f5ff-4612-8b61-ed291d3221e3/video.mp4

## Entry 4
- ID: 15409
- Author: Mo
- Created At: 2026-06-20T01:20:02Z

### Content

I have connected a ring line so the esp32 can wake up whenever the sim800l module receives a message. Also I'm routing the tracks to both the front and back sides of copper layers as my manufacturer doesn't have plated through holes.



for now, I'm still figuring out how the codes will work and there's a lot of undecided things.

### Recording Links

- https://lookout.hackclub.com/api/media/fcdc8102-188f-40f8-956a-141435dee443/video.mp4

## Entry 5
- ID: 15506
- Author: Mo
- Created At: 2026-06-20T07:15:06Z

### Content

Extremely exhausted.
I did the code, made it somewhat basic (no replying to user messages, no measuring for the amount of water poured since I need the sensor to be physically available so I can calibrate the firmware to it). But I believe it is sufficient for now.


### Recording Links

- https://lookout.hackclub.com/api/media/376545c8-d42d-4711-8be1-f17a7eec2e2d/video.mp4

## Entry 6
- ID: 15558
- Author: Mo
- Created At: 2026-06-20T11:34:44Z

### Content

I finished the 3D model. what's left for now is the readme, the zine poster, and some 3D renders for the poster.

Here's how the device looks like:
show case v1.png

### Recording Links

- https://lookout.hackclub.com/api/media/ab6cfb18-3d7e-450d-b56a-0922fbad71be/video.mp4

## Entry 7
- ID: 15587
- Author: Mo
- Created At: 2026-06-20T13:21:14Z

### Content

Me and blender are going through the same thing rn (both of us are crashing out):


Beside that, I have finished the showcase on fusion360 and I might be using this for the poster instead of blender:
show case v5.png
(it's imperfect but I will improve it)

### Recording Links

- https://lookout.hackclub.com/api/media/a747f22e-693e-41f7-b371-261eb6d79cd6/video.mp4

## Entry 8
- ID: 15895
- Author: Mo
- Created At: 2026-06-21T01:42:23Z

### Content

Finished the render!

it was kind of hard as my device is 5 years old with a somewhat dated graphics card, but I managed to work with it!

Here's how the render looks like:


I wanted to add more grass as it would look more realistic but my device can't handle it.

I might modify the texture later and then re-render it. But for now, I'm satisfied with this render.

### Recording Links

- https://lookout.hackclub.com/api/media/40ab7a47-8c26-4372-bd49-37252a3c831d/video.mp4

## Entry 9
- ID: 15911
- Author: Mo
- Created At: 2026-06-21T02:49:51Z

### Content

I modified the texture's a bit so they look better.

I made the water tube transparent, added better color to the wires connected to the probe that's in the soil, and I fixed some things like the cable of the flow sensor being green (made it black), and the screw of the flow sensor were also green (made them black).

Here's what the render looks like:

render 2.png

### Recording Links

- https://lookout.hackclub.com/api/media/63ef874c-4d73-4984-b8f3-b1262206fcad/video.mp4

## Entry 10
- ID: 15968
- Author: Mo
- Created At: 2026-06-21T08:21:33Z

### Content

Added all the required files.

I made sure all the files are available (like the Fusion files, media, etc.)


What's left now is the Zine poster, and the README.

Also made this drawing so reviewers can understand how everything works better:


### Recording Links

- https://lookout.hackclub.com/api/media/1dafa0e2-5839-47d0-afe5-de055ddee4ca/video.mp4

## Entry 11
- ID: 16069
- Author: Mo
- Created At: 2026-06-23T03:46:48Z

### Content

I finished the BOM and changed the 1.6Kohm resistor (that is used with the 555 timer for capacitive soil moisture readings) with a 1.5Kohm resistor. 



The reason I changed it is that I wasn't able to find 1.6Kohm resistors anywhere.

### Recording Links

- https://lookout.hackclub.com/api/media/fbb3ce3d-9b23-4fc6-85db-722628a7d8d8/video.mp4

## Entry 12
- ID: 16192
- Author: Mo
- Created At: 2026-06-25T07:52:30Z

### Content

Finished the zine and the README!

There's nothing much to say for this journal.

Here's the README contents:

Screenshot 2026-06-25 at 10.50.21.png

Here's the zine poster:



### Recording Links

- https://lookout.hackclub.com/api/media/d3a80291-8f6e-4dda-83fb-e65016a85ed3/video.mp4

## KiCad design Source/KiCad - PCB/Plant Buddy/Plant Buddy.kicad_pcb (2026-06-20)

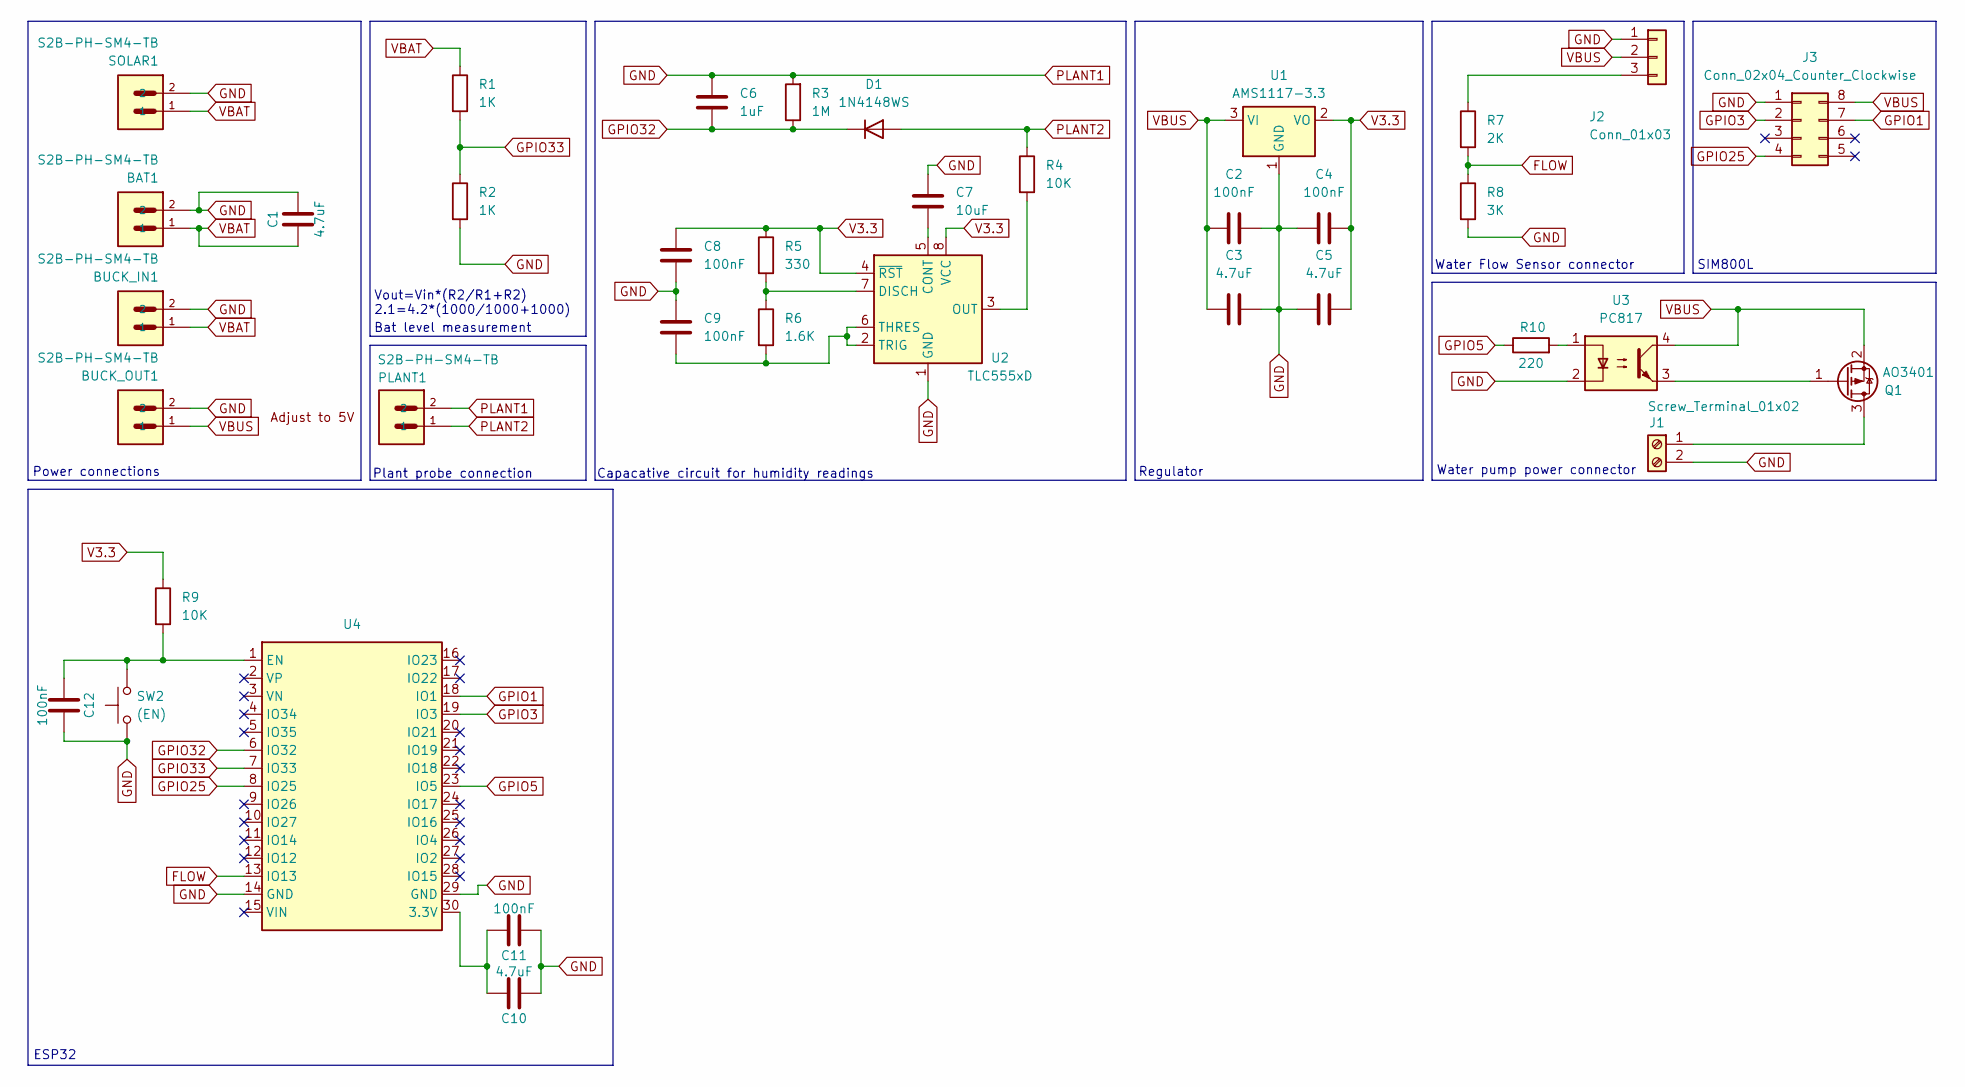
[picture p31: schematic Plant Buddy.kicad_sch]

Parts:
BAT1: S2B-PH-SM4-TB; JST_EH_B2B-EH-A_1x02_P2.50mm_Vertical
BUCK_IN1: S2B-PH-SM4-TB; JST_EH_B2B-EH-A_1x02_P2.50mm_Vertical
BUCK_OUT1: S2B-PH-SM4-TB; JST_EH_B2B-EH-A_1x02_P2.50mm_Vertical
C1, C3, C5, C10: 4.7uF; C_1206_3216Metric_Pad1.33x1.80mm_HandSolder
C2, C4, C8, C9: 100nF; C_0805_2012Metric_Pad1.18x1.45mm_HandSolder
C6: 1uF; C_0805_2012Metric_Pad1.18x1.45mm_HandSolder
C7: 10uF; C_0805_2012Metric_Pad1.18x1.45mm_HandSolder
C11, C12: 100nF; C_1206_3216Metric_Pad1.33x1.80mm_HandSolder
D1: 1N4148WS; D_SOD-323_HandSoldering
J1: Screw_Terminal_01x02; Altech_AK100_1x02_P5.00mm
J2: Conn_01x03; PinSocket_1x03_P2.54mm_Vertical
J3: Conn_02x04_Counter_Clockwise; PinSocket_2x04_P2.54mm_Vertical
PLANT1: S2B-PH-SM4-TB; JST_EH_B2B-EH-A_1x02_P2.50mm_Vertical
Q1: AO3401; SOT-23
R1, R2: 1K; R_0805_2012Metric_Pad1.20x1.40mm_HandSolder
R3: 1M; R_0805_2012Metric_Pad1.20x1.40mm_HandSolder
R4, R9: 10K; R_0805_2012Metric_Pad1.20x1.40mm_HandSolder
R5: 330; R_0805_2012Metric_Pad1.20x1.40mm_HandSolder
R6: 1.6K; R_Axial_DIN0207_L6.3mm_D2.5mm_P7.62mm_Horizontal
R7: 2K; R_0805_2012Metric_Pad1.20x1.40mm_HandSolder
R8: 3K; R_0805_2012Metric_Pad1.20x1.40mm_HandSolder
R10: 220; R_0805_2012Metric_Pad1.20x1.40mm_HandSolder
SOLAR1: S2B-PH-SM4-TB; JST_EH_B2B-EH-A_1x02_P2.50mm_Vertical
SW2: (EN); SW_PUSH_6mm_H13mm
U1: AMS1117-3.3; SOT-223-3_TabPin2
U2: TLC555xD; SOP-8_3.76x4.96mm_P1.27mm
U3: PC817; DIP-4_W7.62mm
U4: ESP32 DevKit

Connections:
FLOW: R7.2, R8.1, U4.13 (IO13)
GND: BAT1.2, BUCK_IN1.2, BUCK_OUT1.2, C1.2, C2.2, C3.2, C4.2, C5.1, C6.2, C7.1, C8.1, C9.1, C10.1, C11.1, C12.2, J1.2, J2.1, J3.1, PLANT1.2, R2.2, R3.2, R8.2, SOLAR1.2, SW2.1, U1.1 (GND), U2.1 (GND), U3.2, U4.14 (GND), U4.29 (GND)
GPIO1: J3.7, U4.18 (IO1)
GPIO3: J3.2, U4.19 (IO3)
GPIO5: R10.1, U4.23 (IO5)
GPIO25: J3.4, U4.8 (IO25)
GPIO32: C6.1, D1.1 (K), R3.1, U4.6 (IO32)
GPIO33: R1.2, R2.1, U4.7 (IO33)
unnamed: J1.1, Q1.3 (D)
unnamed: J2.3, R7.1
unnamed: Q1.1 (G), U3.3
unnamed: R10.2, U3.1
unnamed: C7.2, U2.5 (CONT)
unnamed: R5.2, R6.1, U2.7 (DISCH)
unnamed: R4.2, U2.3 (OUT)
unnamed: C9.2, R6.2, U2.2 (TRIG), U2.6 (THRES)
unnamed: C10.2, C11.2, U4.30 (3.3V)
unnamed: C12.1, R9.2, SW2.2, U4.1 (EN)
PLANT2: D1.2 (A), PLANT1.1, R4.1
V3.3: C4.1, C5.2, C8.2, R5.1, R9.1, U1.2 (VO), U2.4 (~RST), U2.8 (VCC)
VBAT: BAT1.1, BUCK_IN1.1, C1.1, R1.1, SOLAR1.1
VBUS: BUCK_OUT1.1, C2.1, C3.1, J2.2, J3.8, Q1.2 (S), U1.3 (VI), U3.4

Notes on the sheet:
ESP32
Vout=Vin*(R2/R1+R2) 2.1=4.2*(1000/1000+1000)
Water pump power connector
SIM800L
Water Flow Sensor connector
Capacative circuit for humidity readings
Regulator
Plant probe connection
Bat level measurement
Power connections

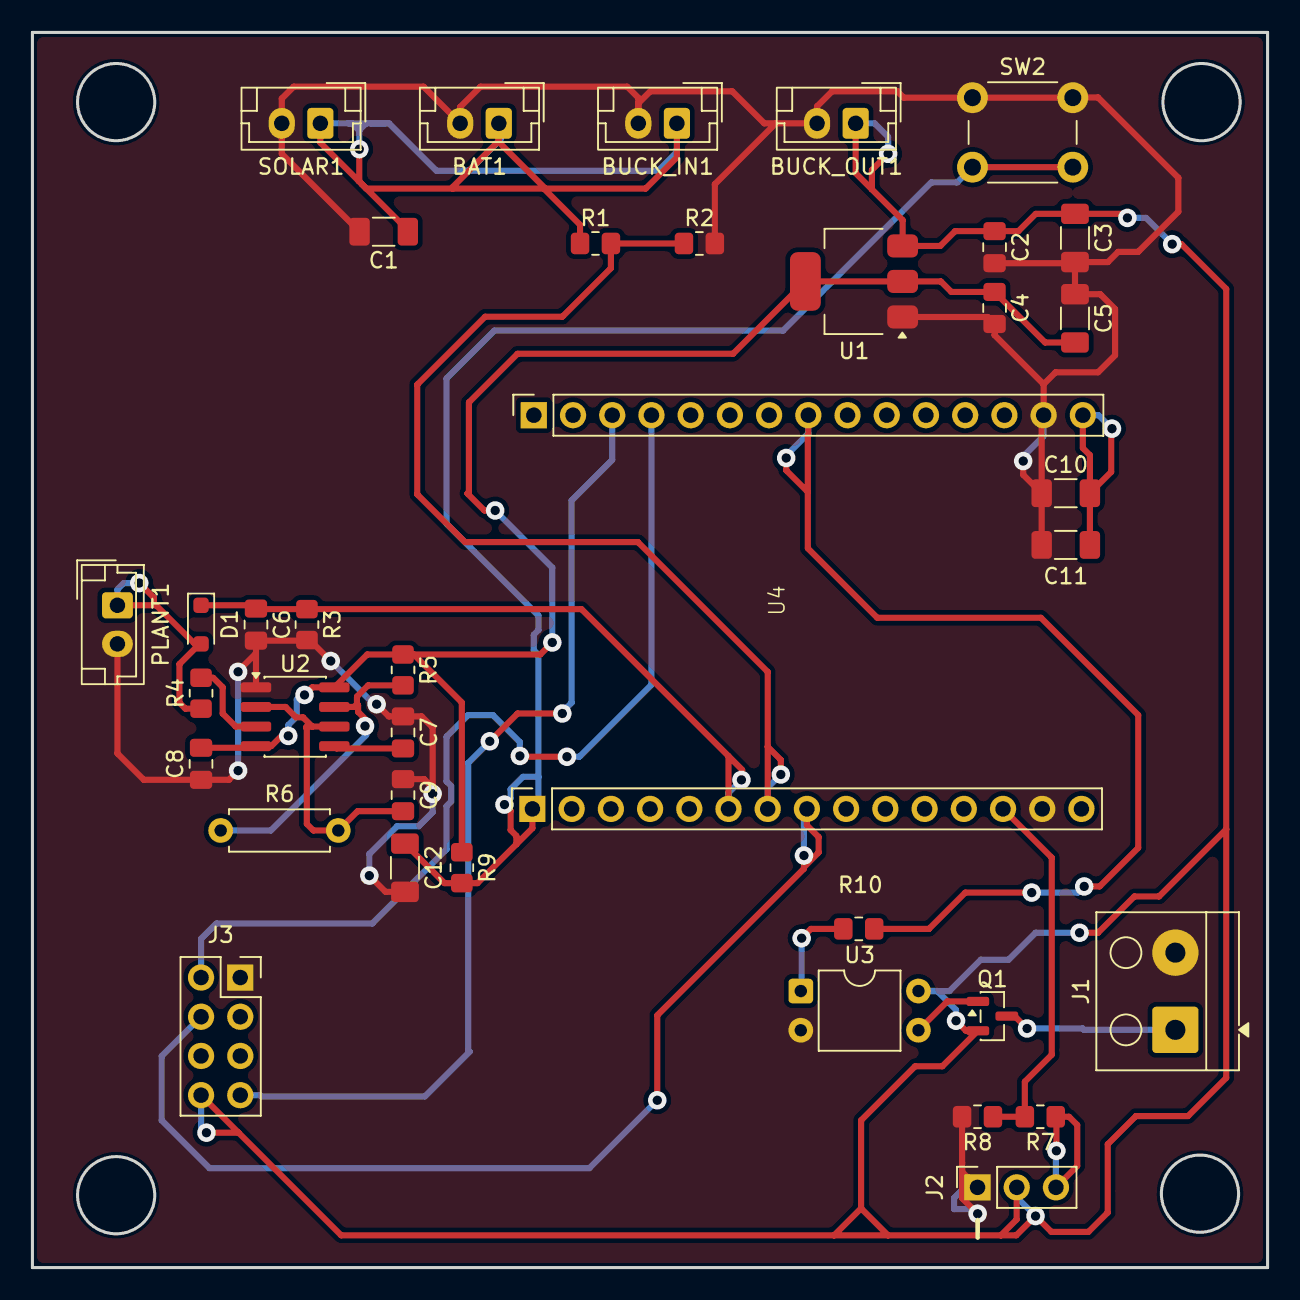
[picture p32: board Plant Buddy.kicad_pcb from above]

Board: 2 copper layers, 80.0 x 80.0 mm, 37 parts (0 on the bottom side), 22 nets.

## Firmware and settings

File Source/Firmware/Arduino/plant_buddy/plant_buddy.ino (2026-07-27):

///////////////////////////////////////////////////////////////////////////////////////////////////////////////////////
// Note to reviewers: I can't imrpove this code as I do not have the hardware available, this is the best I can do.  //
// I'm willing to utilize the flow meter to measure the water in litres and stop at a specified value,               //
// but in order to do so, I need the module physically available in order to calibrate it with known amounts of      //
// water. Also, I will make a function to check if there's no water flow while the pump is running                   //
// which alerts the user that there's no water available, and stops working until told to continue.                  //
// In addition to that, I will be using deep sleep, external interupts (in case user sends a message inquiring       //
// about the device's status), and timer based interupts/wake up. (to water the plant)                               //
// All of this is yet to come in the Plant Buddy V2 firmware.                                                        //
// Thank you for taking the time to review this.                                                                     //
// https://github.com/mkhairyx                                                                                       //
///////////////////////////////////////////////////////////////////////////////////////////////////////////////////////

#include <Preferences.h>

Preferences prefs;

String number = "+xxxxxxxxxxxx"; // Owner's phone number

#define Battery 33 // Use your specific ADC GPIO pin
#define soil 32
#define pump 5
#define period 20 // 20 days (max 30 days)
#define wet 1000
#define dry 2000
 

unsigned long water_interval; // days in ms
int water_time = 5000; // for now, I will be watering the plant for 5 seconds. In V2, I'll use the flow sensor.
int BATP; // battery percentage
int humidity;
unsigned long days;

/*
gpio 33 for battery voltage - no pinMode() needed as it's attached to the adc
gpio 32 for soil readings - no pinMode() needed as analogread() is used
gpio 5 for pump motor - pinMode(pump, OUTPUT);
gpio 3 for gsm_tx -
gpio 1 for gsm_rx -
gpio 13 for flow 
gpio 25 for ring ping 
*/



void setup() 
{
  pinMode(pump, OUTPUT);
  digitalWrite(pump, LOW);
  prefs.begin("periodic", false);
  if (prefs.getInt("cause", 2) == 2)
  {
    delay(30000); //delay for 30 seconds to make sure the module boots up
  }
  Serial.begin(9600);
  analogSetPinAttenuation(Battery, ADC_6db);
  analogSetWidth(12);
  BATP = constrain(((analogRead(Battery)*100)/3908), 0, 100); // battery percentages
  humidity = constrain(map(analogRead(soil), dry, wet, 0, 100), 0, 100);
  days = period;
  // Send message with values:
  Serial.println("AT+CMGF=1");    //Sets the GSM Module in Text Mode
  Serial.println("AT+CMGS=\"" + number + "\"\r"); //Mobile phone number to send message
  delay(500);
  Serial.println("The device just booted up!");
  Serial.print("The battery is at ");
  Serial.println(BATP);
  Serial.println("%");
  Serial.print("The soil humidity is ");
  Serial.print(humidity);
  Serial.println("%");
  Serial.print("The period between each time the plant is watered is ");
  Serial.print(days);
  Serial.println(" days.");
  Serial.print("The boot cause was ");
  switch (prefs.getInt("cause", 2)) {
    case 0: // faulty restart
        Serial.println("an unknown fault...");
        break;
    case 1: // on purpose restart.
        Serial.println("new cycle started (just finished watering!).");
        Serial.println("Watering again in ");
        Serial.print(days);
        Serial.println(" days.");
        break;
    case 2:
        Serial.println("First boot!");
        break;
    default:
        Serial.println("N/A. Please contact the firmware provider.");
        break;
  }
  Serial.print((char)26); // SEND MESSAGE (ASCII FOR CTRL+Z)
  if (prefs.getInt("cause", 2) == 2) // First boot!
  {
    digitalWrite(pump, HIGH);
    delay(water_time);
    digitalWrite(pump, LOW);
  }
  prefs.putInt("cause", 0); // if anything happens (as an undervoltage or system shutdown during the delay, the boot/restart cause will be an unknown fault, ie case 0)
  prefs.end();
  water_interval = days * 86400000;  // = 24 hours * 60 mins * 60 secs * 1000 ms
}

void loop() 
{               
  if (millis() >= water_interval) // using millis to allow multitasking in future version of this code. 
  {
    prefs.begin("periodic", false);
    prefs.putInt("cause", 1); // restarting to water the plant
    prefs.end();
    // int asap = millis();
    digitalWrite(pump, HIGH);
    delay(water_time);
    digitalWrite(pump, LOW);
    ESP.restart();
  }
  // future multi tasking stuff (like user calling for status), or maybe I will put the esp into deep sleep and use interupts.
}

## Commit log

2026-06-17 Added KiCad files
    [Plant Buddy.kicad_pcb, Plant Buddy.kicad_sch]
2026-06-17 Added water flow sensor connector
    [Plant Buddy.kicad_sch]
2026-06-17 Kicad saved
2026-06-18 Finished Schematic and PCB
    [Plant Buddy.kicad_pcb, Plant Buddy.kicad_sch, esp32_dev_kit_v1_asm.stp]
2026-06-19 Edited PCB and schematics.
    [Plant Buddy.kicad_pcb, Plant Buddy.kicad_sch]
2026-06-20 Finished the firmware and modified the schematics and the PCB
    [Plant Buddy.kicad_pcb, Plant Buddy.kicad_sch]
2026-06-20 Firmware uploaded
    [partitions.csv]
2026-06-20 Designed 3D case
    [Case_and_barbs.step, KF301-2P--3DModel-STEP-510211.STEP, PCB_bom.csv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]
2026-06-21 Added more project files
    [PCB_bom.csv, PCB_designators.csv, PCB_positions.csv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]
2026-06-22 Added BOM
    Added the BOM, and modified the schematics to have a resistor that I can buy.
    [BOM.csv, Plant Buddy (KiCad).csv, Plant Buddy.kicad_sch]
2026-06-25 Removed firmware from the Arduino folder
    [partitions.csv]
2026-06-25 README, BOM, Code were changed
    Added a README, changed the BOM with the correct info, modified the code to print % next to the battery percentage, and added a picture of a quote from JLCPCB
    [BOM.csv]
